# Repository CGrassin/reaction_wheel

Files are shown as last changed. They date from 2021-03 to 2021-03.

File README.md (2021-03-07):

# Reaction Wheel model

This repository contains the files (code and STL) to build a reaction wheel controlled satellite model.

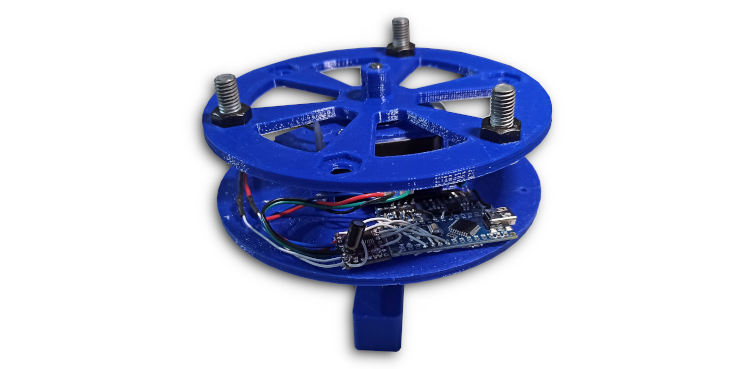
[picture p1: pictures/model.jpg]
The satellite model


This project is described in this article (including test results): https://charleslabs.fr/en/project-Reaction+Wheel+Attitude+Control

## Material

There are 4 parts to 3D-print: base, satellite disk, motor holder and flywheel. The only part requiring support is the motor holder.

Additionnal hardware is required:

| Quantity  | Item |
|---|---|
| 1 | NEMA 17 (23&nbsp;mm or 40&nbsp;mm length) |
| 2 | 608 bearing |
| 1 | M8 threaded rod (65&nbsp;mm) |
| 4 | M8 nut |
| 8 | M3&times;6&nbsp;mm screw |
| 4 | M3 nut |
| 1 | Arduino Nano board |
| 1 | DRV8825 driver module |
| 1 | Level shifter module |
| 1 | MPU6050 sensor module |
| 1 | 100&nbsp;µF 16&nbsp;V capacitor |
| 1 | 2S LiPo Battery (300&nbsp;mAh) |

Additionnal M8 hardware is required to tune the moment of inertia of the wheel. In my case, I used 3 M8&times;20&nbsp;mm bolts and 3 M8 nuts.

See the article for more detailed build instructions.

## License

This model is released under the terms of the MIT License.

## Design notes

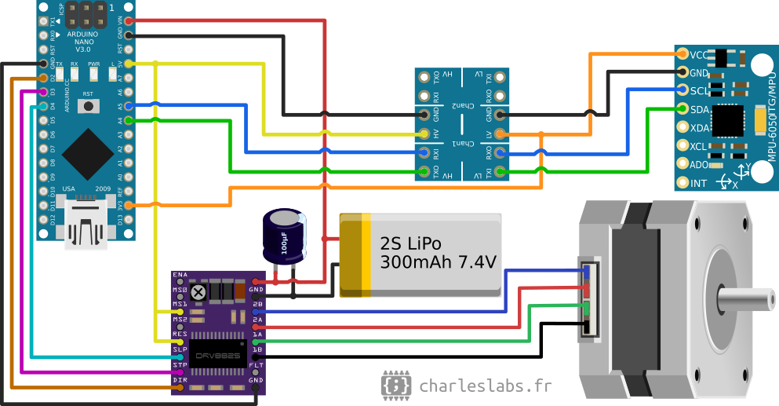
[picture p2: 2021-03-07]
Electronics/RW2_circuit.png

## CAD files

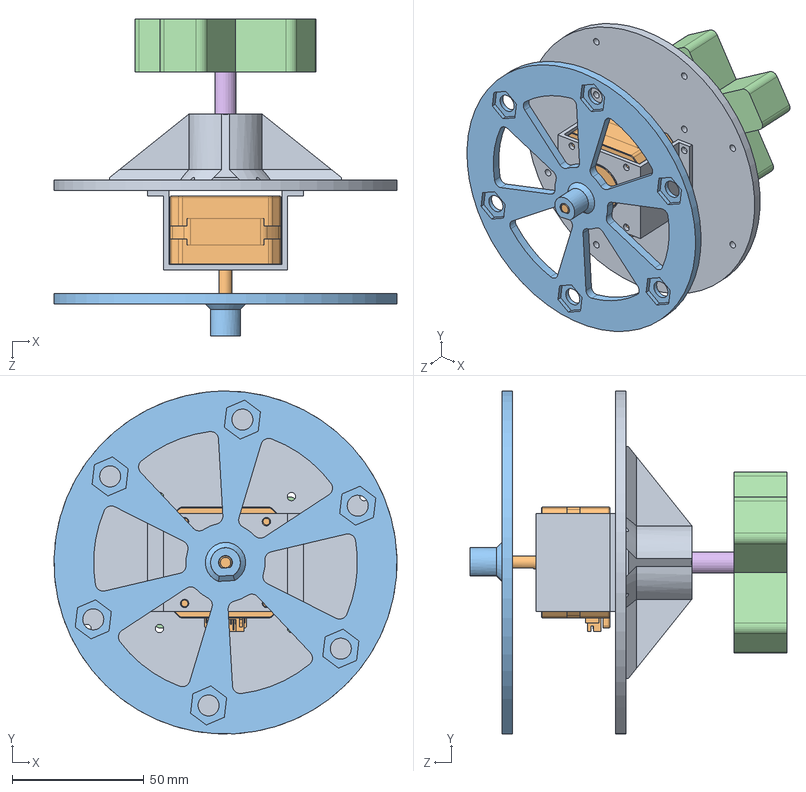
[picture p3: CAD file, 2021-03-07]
CAD_ReactionWheel/SolidWorks_src/Assembly/RW_Assembly.SLDASM
130.0 x 130.0 x 120.0 mm
RW_Satellite
E3D Slimline Stepper Motor 0.9deg V1.1
RW_Flywheel
RW_Base
8mm Bearing SKF 608 (RS 286-7530) x 2
8mm_threaded_rod

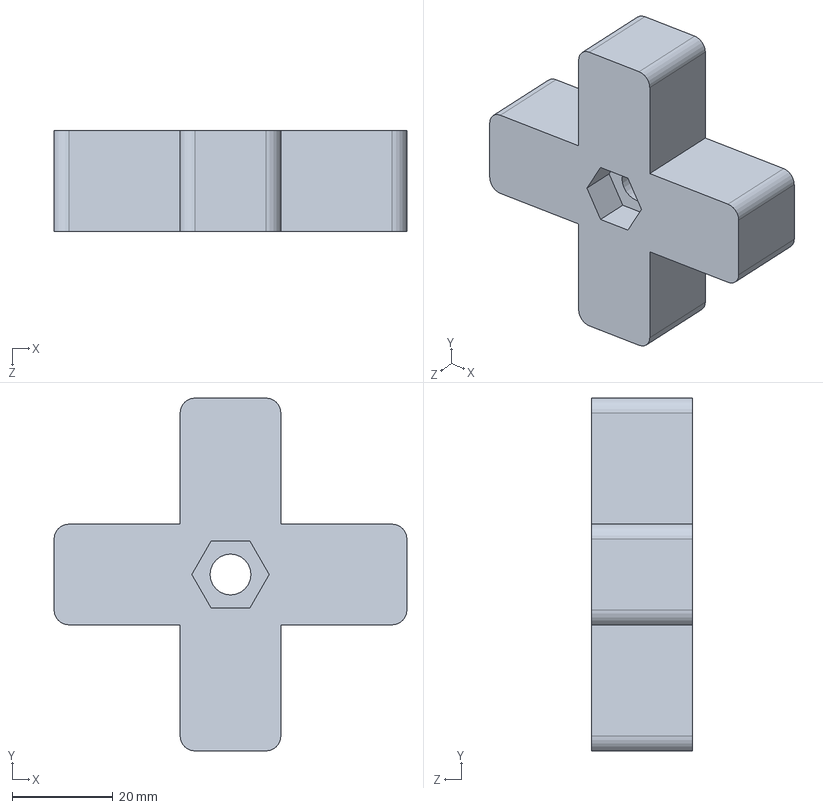
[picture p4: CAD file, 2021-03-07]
CAD_ReactionWheel/SolidWorks_src/RW_Base.SLDPRT
70.0 x 70.0 x 20.0 mm

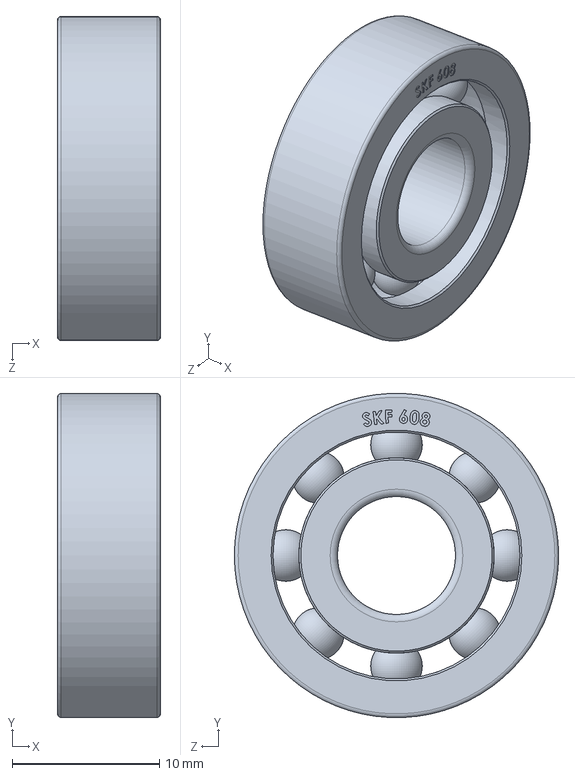
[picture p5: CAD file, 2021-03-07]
CAD_ReactionWheel/SolidWorks_src/Assembly/8mm Bearing SKF 608 (RS 286-7530).SLDPRT
7.00 x 22.0 x 22.0 mm

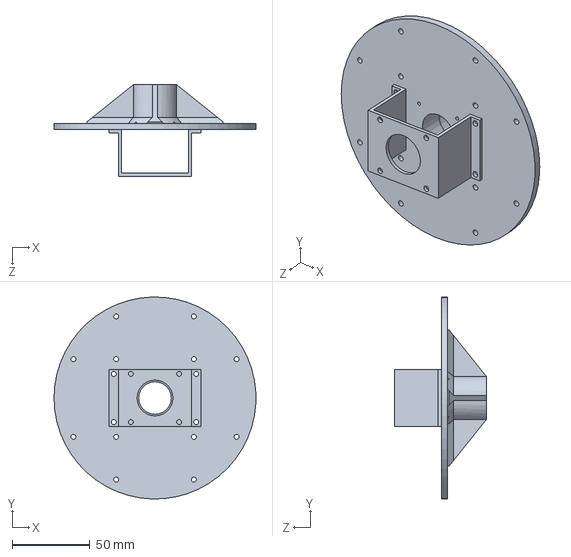
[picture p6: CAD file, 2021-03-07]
CAD_ReactionWheel/SolidWorks_src/RW_Satellite.SLDPRT
130.0 x 129.9 x 59.0 mm

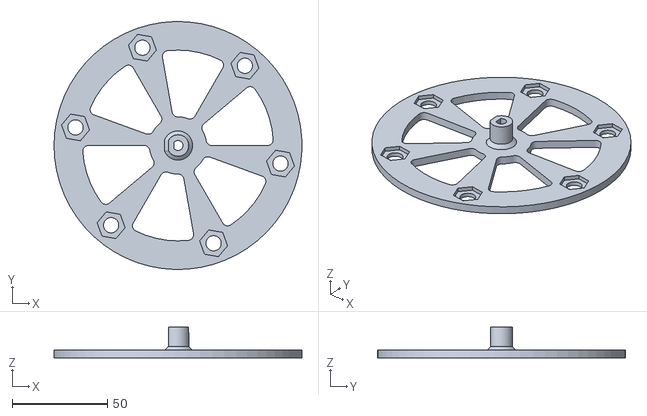
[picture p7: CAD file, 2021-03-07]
CAD_ReactionWheel/STL_files/RW_Flywheel.STL
130.0 x 130.0 x 16.0

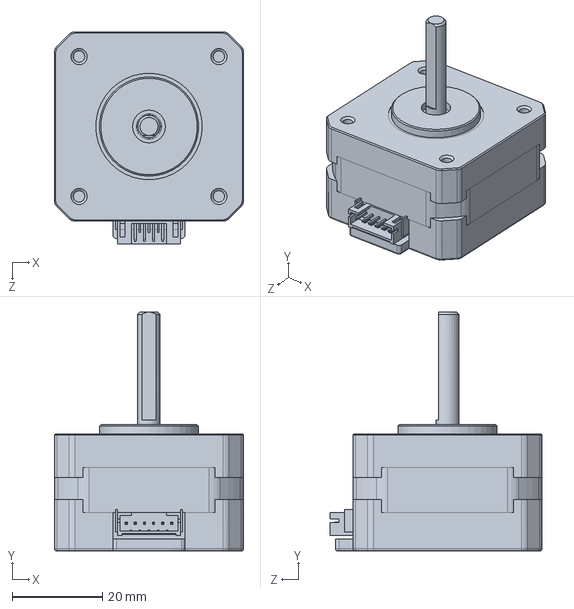
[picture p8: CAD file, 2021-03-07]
CAD_ReactionWheel/SolidWorks_src/Assembly/E3D Slimline Stepper Motor 0.9deg V1.1.SLDPRT
42.0 x 53.0 x 47.1 mm

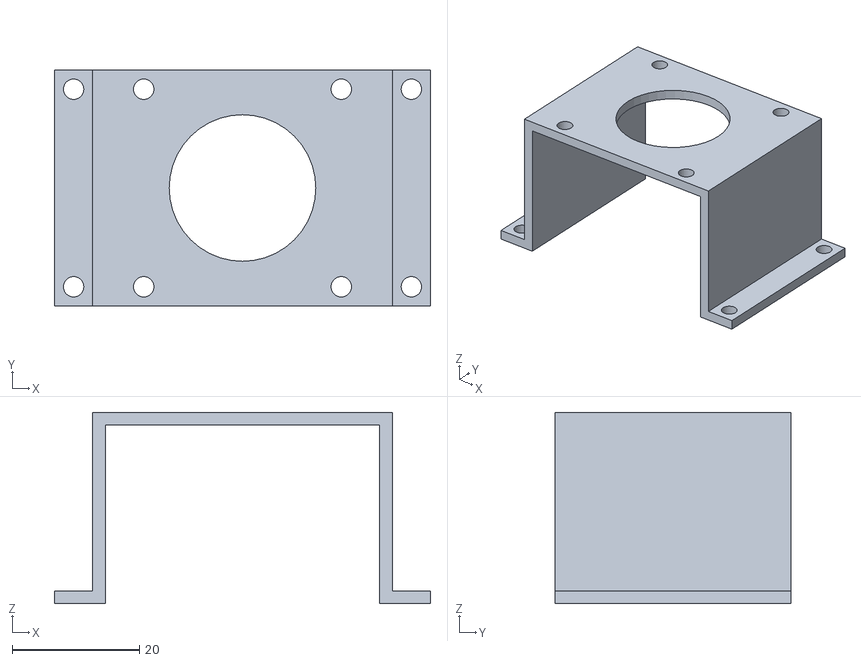
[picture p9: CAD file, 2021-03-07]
CAD_ReactionWheel/STL_files/RW_Satellite-MotorHolder_26mm.STL
59.0 x 37.0 x 30.0

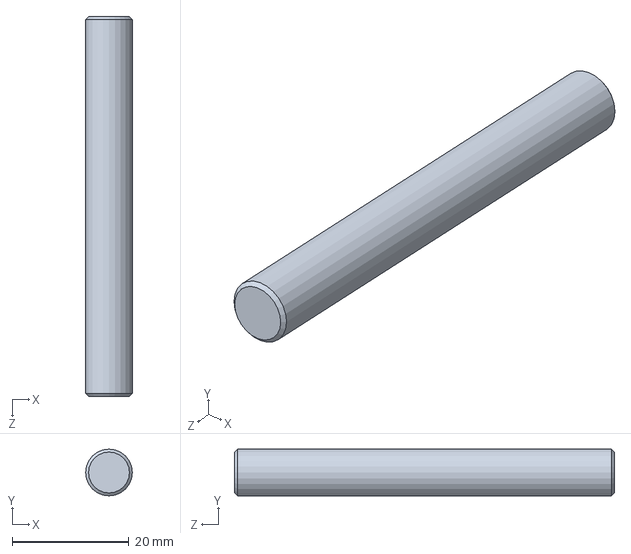
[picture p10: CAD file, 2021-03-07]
CAD_ReactionWheel/SolidWorks_src/Assembly/8mm_threaded_rod.SLDPRT
8.00 x 8.00 x 65.0 mm

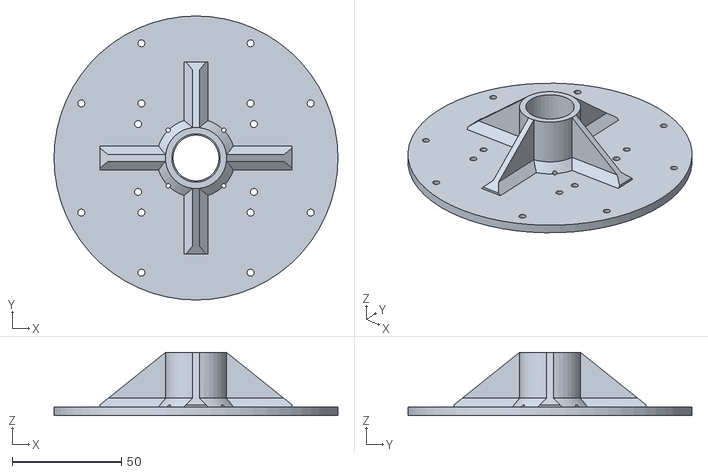
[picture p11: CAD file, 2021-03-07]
CAD_ReactionWheel/STL_files/RW_Satellite-Disk.STL
130.0 x 130.0 x 29.0

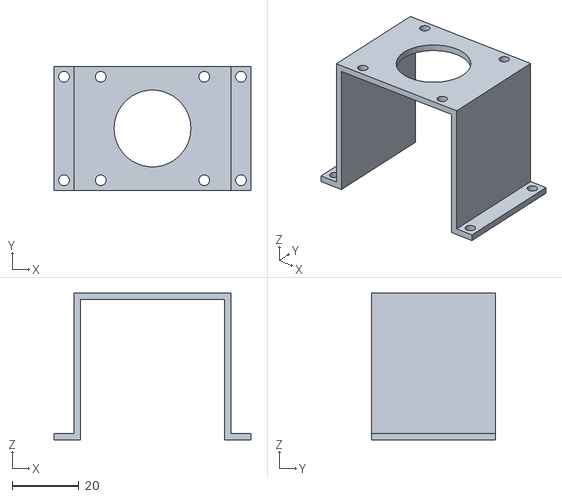
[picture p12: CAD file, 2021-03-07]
CAD_ReactionWheel/STL_files/RW_Satellite-MotorHolder_40mm.STL
59.0 x 37.0 x 44.0

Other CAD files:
CAD_ReactionWheel/SolidWorks_src/RW_Assembly.STEP
CAD_ReactionWheel/STL_files/RW_Base.STL
CAD_ReactionWheel/SolidWorks_src/RW_Flywheel.SLDPRT

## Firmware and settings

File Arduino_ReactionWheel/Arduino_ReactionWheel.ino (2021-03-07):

/*
 * This is the controller code for the reaction wheel satellite model published
 * at https://charleslabs.fr/en/project-Reaction+Wheel+Attitude+Control
 *
 * The electronics diagram and the mechanical build is described in this article.
 *
 * You can set the PID controller terms and various other parameters hereunder.
 *
 * Charles GRASSIN, 2021
 * MIT License
 */

#define SERIAL_DEBUG_ENABLE 1 /* 0 = disable, 1 = enable */
#define MPU6050_CALIBRATION 0 /* 0 = disable, 1 = enable */
#define CONTROLLER_MODE 0 /* 0 = Speed stabilization only, 1 = Speed and Attitude stabilization, 2 = same as 1, but change set point every N secondes */

// -------PINS-------
#define PIN_DIR    2
#define PIN_STEP   3
#define PIN_SLEEP  4
#define PIN_LED    13
// ------------------

// -----STEPPER------
#include "AccelStepper.h" // This is a hacked version of this library to allow
                          // speed control instead of position control.
AccelStepper myStepper(1, PIN_STEP, PIN_DIR);
double motorSpeed = 0;
#define MICROSTEPPING 4 /* 1 or 2 or 4 or 8 or 16 or 32 */
#define ACCELERATION 1750 /* Steps per s */
#define MAX_SPEED (600 * MICROSTEPPING)
// ------------------

// -------PID--------
#include "PID.h"
const double P_TERM = 0.050 * MICROSTEPPING;
const double I_TERM = 0.000 * MICROSTEPPING;
const double D_TERM = 0.017 * MICROSTEPPING; 
PIDController pidSpeed(P_TERM, I_TERM, D_TERM);
PIDAngleController pidAttitude(2.5, 0, 400);
// ------------------

// ------MPU6050-----
#include <Wire.h>
#define MPU_ADDRESS 0x68   // I2C address of the MPU-6050
double GYRO_ERROR = 61.96; // rollingAvg error compensation
double yawAngle=0, yawAngularSpeed=0;
// ------------------

// ------GENERAL-----
long timeCur, timePrev, timeStart; 
const int numReadings= 5;
double readings[numReadings];
int readIndex = 0;
double total = 0, rollingAvg = 0;
double targetAttitude = 0;
// ------------------

void setup() {
  #if SERIAL_DEBUG_ENABLE == 1
    Serial.begin(115200);
    delay(500);
    Serial.println("Attitude Speed");
  #endif
  
  // Gyro setup
  Wire.begin();
  Wire.beginTransmission(MPU_ADDRESS);
  Wire.write(0x6B);  // PWR_MGMT_1 register
  Wire.write(0);     // wakes up the MPU-6050
  Wire.endTransmission(true);
  Wire.beginTransmission(MPU_ADDRESS);
  Wire.write(0x1B); // GYRO_CONFIG register
  Wire.write(0x10); // 1000dps full scale
  Wire.endTransmission(true);

  // Gyro cal (only if selected, otherwise use saved value)
  #if MPU6050_CALIBRATION == 1
    calibrateMPU();
  #endif

  // LED
  pinMode(PIN_LED,OUTPUT);
  digitalWrite(PIN_LED,1);
  
  // Initial stepper parameters
  myStepper.setEnablePin (PIN_SLEEP);
  myStepper.setAcceleration(ACCELERATION);
  setSpeedStepper(0);
  
  timeCur = millis();
  timeStart = timeCur;
}

// FSM variables
byte controllerState = 0;
int counts = 0;

// Main loop
void loop() {
  // Stop control after 40s
  // if(millis() - timeStart > 40000){
  //   digitalWrite(PIN_LED,0);
  //   myStepper.disableOutputs ();
  // }
  
  // Pulse stepper
  myStepper.run();

  // Every 10ms, read MPU and call controllers
  if(millis() - timeCur > 10) {
    timePrev = timeCur;
    timeCur = millis();

    // Measure Gyro value
    yawAngularSpeed = ((double)readMPU()-GYRO_ERROR) / 32.8;
    yawAngle += (yawAngularSpeed * (timeCur - timePrev) / 1000.0);
    // Put angle between -180 and 180
    while (yawAngle <= -180) yawAngle += 360; 
    while (yawAngle > 180)   yawAngle -= 360;

    // Low Pass Filter the angular speed (https://www.arduino.cc/en/Tutorial/BuiltInExamples/Smoothing)
    total = total - readings[readIndex]; 
    readings[readIndex] = yawAngularSpeed;
    total = total + readings[readIndex];
    readIndex = readIndex + 1;
    if (readIndex >= numReadings)
      readIndex = 0;
    rollingAvg = total / numReadings; 

    // Compute controller output
    #if CONTROLLER_MODE == 0
      // Detumbling only
      motorSpeed += pidSpeed.compute(0,rollingAvg,timeCur - timePrev);
    #else if CONTROLLER_MODE == 1 || CONTROLLER_MODE == 2
      // Change set point
      #if CONTROLLER_MODE == 2
        counts ++;
        if(counts == 250) {
          counts = 0;
          if(targetAttitude == 0)
            targetAttitude = 180;
          else
            targetAttitude = 0;
        }
      #endif
      
      // FSM transition
      if(controllerState == 1 &&  fabs(rollingAvg) > 360 /* °/s */){
        controllerState = 0;digitalWrite(PIN_LED,0);
      }
      else if(controllerState == 0 && fabs(rollingAvg) < 45 /* °/s */)
        controllerState = 1;
      
      //FSM action
      if(controllerState == 0){
        motorSpeed += pidSpeed.compute(0,rollingAvg,timeCur - timePrev);
        pidAttitude.compute(targetAttitude,yawAngle,timeCur - timePrev);
      }
      else
        motorSpeed += pidSpeed.compute(pidAttitude.compute(targetAttitude,yawAngle,timeCur - timePrev),rollingAvg,timeCur - timePrev);
    #endif

    // Constrain speed to valid interval (saturation)
    if(motorSpeed > MAX_SPEED) motorSpeed = MAX_SPEED;
    else if (motorSpeed < -MAX_SPEED) motorSpeed = -MAX_SPEED;
    
    setSpeedStepper(motorSpeed);

    // Report attitude and speed
    #if SERIAL_DEBUG_ENABLE == 1
      Serial.print(yawAngle);
      Serial.print(" ");
      Serial.println(rollingAvg);
    #endif
  }
}

// Set the current speed and direction of the motor
void setSpeedStepper(double targetSpeed){
  if(targetSpeed > 0)
    myStepper.moveTo(1000000);
  else 
    myStepper.moveTo(-1000000);

  myStepper.setMaxSpeed(fabs(targetSpeed));
}

// Read a yaw angular speed value
int16_t readMPU(){
  Wire.beginTransmission(MPU_ADDRESS);
  Wire.write(0x47);
  Wire.endTransmission(false);
  Wire.requestFrom(MPU_ADDRESS,2,true);
  return Wire.read()<<8|Wire.read();  // 0x47 (GYRO_ZOUT_H) & 0x48 (GYRO_ZOUT_L)
}

// Calibrate the gyro by doing CALIBRATION_MEASUREMENTS_COUNT measurements
#define CALIBRATION_MEASUREMENTS_COUNT 200
void calibrateMPU(){
  GYRO_ERROR = 0;
  for(int i=0;i<CALIBRATION_MEASUREMENTS_COUNT;i++){
    GYRO_ERROR += readMPU();
    delay(20);
  }
  GYRO_ERROR = GYRO_ERROR/(double)CALIBRATION_MEASUREMENTS_COUNT;
  #if SERIAL_DEBUG_ENABLE == 1
    Serial.println(GYRO_ERROR);
  #endif
}
